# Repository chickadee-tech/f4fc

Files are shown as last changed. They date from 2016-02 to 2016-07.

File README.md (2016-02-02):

# Chickadee Tech F4FC #
This an STM32F4-based flight control Polystack board for multirotors designed by Chickadee Tech. It features an STM32F405VGT6 microcontroller and an MPU-6000 accelerometer/gyroscope. It runs a modified version of [Betaflight](https://github.com/betaflight/betaflight) available [here](github.com/chickadee-tech/betaflight) with the CKD_F4FC target.

## Documentation ##
See the [wiki](https://github.com/chickadee-tech/f4fc/wiki) for documentation.

## Polystack ##
This **control** board is part of the Polystack platform for modular microcontrol systems. More information on the platform can be found at [polystack.org](http://polystack.org).

## Support ##
If you need support with a board you own or have development questions please email support@chickadee.tech or check [chickadee.tech/support](https://chickadee.tech/support) for other ways to get support.

## Contributing ##
Please note that this project is released with a [Contributor Code of Conduct](CODE_OF_CONDUCT.md). By participating in this project you agree to abide by its terms.

### Setup ###
Components and footprints for PCB parts are not included in this repository. Instead, checkout the [chickadee-tech/kicad-libs](https://github.com/chickadee-tech/kicad-libs) repository in the same directory that this repository is checked out in. All part definitions should be relative so that they will load correctly.

### Pull requests ###
For fixes please submit a pull request to the original repository. After the pull request is merged, check the [Chickadee Tech Active Contributor Discount (ACD)](https://chickadee.tech/active-contributor) to see if you are eligible for a discount code to use on your next purchase.

### Derivatives ###
If developing your own version of the F4FC please remove all Chickadee Tech trademarks and follow the [CC-BY license](LICENSE). While not required, please consider open sourcing your modifications so others can learn from your improvements. If you do email support@chickadee.tech and we may choose to add your project to the ACD.

You may also license the Polystack logo for free by emailing support@chickadee.tech. We'll ask for your gerbers to ensure the design complies with specifications laid out [here](https://github.com/chickadee-tech/polystack/wiki) and provide written permission to use the trademark after compliance has been demonstrated.

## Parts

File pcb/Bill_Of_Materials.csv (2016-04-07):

part name | symbol | size (imp) | max current | unit price | units per build | units in stock | On Order | order total | Manufacturer ID | source url | MacroFab HP | datasheet | datasheet2
C 0.1uF | C1, C4, C6, C7, C8, C10, C13 | 603 |  | $0.02 | 7 | 400 | SMD Binder - Capacitors | $0.15 | C0603C104K4RACTU | http://www.digikey.com/product-detail/en/C0603C104K4RACTU/399-1096-1-ND/411371 |  | MF-CAP-0603-0.1uF | http://www.kemet.com/docfinder?Partnumber=C0603C104K4RACTU
C 4.7uF | C2 |  |  | $0.05 | 1 | 8 | SMD Binder - Capacitors | $0.05 | C0603C475K9PACTU | http://www.digikey.com/product-detail/en/C0603C475K9PACTU/399-3482-1-ND/754775 | http://www.mouser.com/ProductDetail/Kemet/C0603C475K9PACTU/ | N
C 2.2nF (2200pF) X7R 50V | C3 | 603 |  | $0.01 | 1 | 94 | SMD Binder - Capacitors | $0.01 | C0603C222K5RACTU | http://www.digikey.com/product-detail/en/C0603C222K5RACTU/399-1085-1-ND/411360 | http://www.mouser.com/ProductDetail/Kemet/C0603C222K5RACTU/?qs=sGAEpiMZZMs0AnBnWHyRQFqPnX0OlvcoEeor2YsHDUE%3d | N
C 2.2uF | C9, C14, C15 | 603 |  | $0.05 | 3 | 92 | SMD Binder - Capacitors | $0.14 | C0603C225K9PACTU | http://www.digikey.com/product-detail/en/C0603C225K9PACTU/399-3362-1-ND/650351 | http://www.mouser.com/ProductDetail/Kemet/C0603C225K9PACTU/?qs=sGAEpiMZZMs0AnBnWHyRQJIiGvDVk92V8FIBbbmgLZk%3d
C 1uF X7R | C5, C12 | 603 |  | $0.03 | 2 | 20 | SMD Binder - Capacitors | $0.06 | TMK107B7105KA-T | http://www.digikey.com/product-detail/en/TMK107B7105KA-T/587-2984-1-ND/2714177 |  | MF-CAP-0603-1uF | http://ds.yuden.co.jp/TYCOMPAS/ut/detail.do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
C 10uF X5R | C11 | 1206 |  | $0.24 | 1 | 80 | SMD Binder - Capacitors | $0.24 | C3216X5R1C106M160AA | http://www.digikey.com/product-detail/en/C3216X5R1C106M160AA/445-1426-1-ND/569092 |  | MF-CAP-1206-10uF | http://product.tdk.com/en/catalog/datasheets/mlcc_commercial_general_en.pdf
red led | D3, D5 |  |  | $0.19 | 2 | 71 | SMD Binder - Diodes | $0.37 | LTST-C190KRKT | http://www.digikey.com/product-detail/en/LTST-C190KRKT/160-1436-1-ND/386816 |  | MF-LED-0603-RED | http://optoelectronics.liteon.com/upload/download/DS-22-99-0151/S_110_LTST-C190KRKT.pdf
yellow led | D2 |  |  | $0.20 | 1 | 87 | SMD Binder - Diodes | $0.20 | LTST-C190KSKT | http://www.digikey.com/product-detail/en/LTST-C190KSKT/160-1437-1-ND/386818 |  | N | http://optoelectronics.liteon.com/upload/download/DS-22-99-0189/S_110_LTST-C190KSKT.pdf
green led | D1 |  |  | $0.19 | 1 | 83 | SMD Binder - Diodes | $0.19 | LTST-C190KGKT | http://www.digikey.com/product-detail/en/LTST-C190KGKT/160-1435-1-ND/386814 |  | Y | http://optoelectronics.liteon.com/upload/download/DS22-2000-074/S_110_LTST-C190KGKT.pdf
Power OR Diode | D4 |  | 500mA | $0.49 | 1 | 6 | SMD Binder - Diodes | $0.49 | PMEG2005CT,215 | http://www.digikey.com/product-detail/en/PMEG2005CT,215/568-6500-1-ND/2531787 | http://www.mouser.com/ProductDetail/NXP/PMEG2005CT215/ | N | http://www.nxp.com/documents/data_sheet/PMEG2005CT.pdf
~3.5mm Spacer | Off Board |  |  | $0.08 | 4 | 81 | SMD Binder - Connectors | $0.33 | 908-140 | http://www.mouser.com/search/ProductDetail.aspx?R=0virtualkey0virtualkey908-140 |  | N
Nylon Hex Nut | Off Board |  |  | $0.10 | 8 | 94 | SMD Binder - Connectors | $0.76 | 4688 | http://www.mouser.com/ProductDetail/Keystone-Electronics/4688/ |  | N
usb otg | P3 |  | 500mA | $0.46 | 1 | 7 | SMD Binder - Connectors | $0.46 | 10118193-0001LF | http://www.digikey.com/product-detail/en/10118193-0001LF/609-4616-1-ND/2785380 | http://www.mouser.com/ProductDetail/FCI/10118193-0001LF/ | MF-CON-MICROUSB-RIGHT
2x4 right angle | P4 |  |  | $0.80 | 1 | 2 | SMD Binder - Connectors | $0.80 | 5-102975-4 |  | http://www.mouser.com/ProductDetail/TE-Connectivity-AMP/5-102975-4/ | N
80 pin receptacle (3.5mm) | CKD_SANDWICH |  | 0.3A a pin | $2.42 | 1 | 1 | SMD Binder - Connectors | $2.42 | DF40HC(3.5)-80DS-0.4V(51) | http://www.digikey.com/product-detail/en/DF40HC(3.5)-80DS-0.4V(51)/H11997CT-ND/2880228 | http://www.mouser.com/ProductDetail/Hirose-Electric/DF40HC35-80DS-04V51/ | N | http://www.hirose.co.jp/cataloge_hp/ed_DF40_20140305.pdf
20pin hirose header | P5 |  | 0.3A a pin | $0.79 | 1 | 7 | SMD Binder - Connectors | $0.79 | DF40C-20DP-0.4V(51) | http://www.digikey.com/product-detail/en/DF40C-20DP-0.4V(51)/H11618CT-ND/1969498 | http://www.mouser.com/ProductDetail/Hirose-Electric/DF40C-20DP-04V51/ | N | http://www.hirose.co.jp/cataloge_hp/ed_DF40_20140305.pdf
Chickadee F4FC v1 | PCB |  |  | $6.73 | 1 | 3 | PCB | $6.73 | CKD-F4FC-V1 |  |  | N
p-channel mosfet | Q1 | TO-236-3, SC-59, SOT-23-4 | 220mA continuous | $0.10 | 1 | 97 | SMD Binder - ICs | $0.10 | BSS84 | http://www.digikey.com/product-detail/en/fairchild-semiconductor/BSS84/BSS84CT-ND/244297 | http://www.mouser.com/search/ProductDetail.aspx?R=0virtualkey0virtualkeyBSS84 | MF-DSC-SOT233-BSS84 | https://www.fairchildsemi.com/datasheets/BS/BSS84.pdf
n-channel mosfet | Q3, Q4 | TO-236-3, SC-59, SOT-23-3 | 220mA continuous | $0.09 | 2 | 59 | SMD Binder - ICs | $0.19 | BSS138 | http://www.digikey.com/product-detail/en/BSS138/BSS138CT-ND/244294 |  | MF-DSC-SOT233-BSS138 | https://www.fairchildsemi.com/datasheets/BS/BSS138.pdf
R 1k | R1, R2, R3, R12 | 603 |  | $0.01 | 4 | 993 | SMD Binder - Resistors | $0.04 | RC0603FR-071KL | http://www.digikey.com/product-detail/en/RC0603FR-071KL/311-1.00KHRCT-ND/729790 |  | MF-RES-0603-1K | http://www.yageo.com/NewPortal/yageodocoutput?fileName=/pdf/R-Chip/PYu-RC_Group_51_RoHS_L_3.pdf
R 10k | R4, R5, R8 | 603 |  | $0.01 | 3 | 979 | SMD Binder - Resistors | $0.03 | RC0603FR-0710KL | http://www.digikey.com/product-detail/en/RC0603FR-0710KL/311-10.0KHRCT-ND/729827 |  | MF-RES-0603-10K | http://www.yageo.com/NewPortal/yageodocoutput?fileName=/pdf/R-Chip/PYu-RC_Group_51_RoHS_L_3.pdf
R 4.7k | R6, R7 | 1206 |  | $0.01 | 2 | 68 | SMD Binder - Resistors | $0.01 | RC0603FR-074K7L | http://www.digikey.com/product-detail/en/RC0603FR-074K7L/311-4.70KHRCT-ND/730159 |  | MF-RES-0603-5.6K | http://www.yageo.com/NewPortal/yageodocoutput?fileName=/pdf/R-Chip/PYu-RC_Group_51_RoHS_L_3.pdf
R 470k | R9 | 603 |  | $0.01 | 1 | 68 | SMD Binder - Resistors | $0.01 | RC0603FR-07470KL | http://www.digikey.com/product-detail/en/RC0603FR-07470KL/311-470KHRCT-ND/730204 |  | MF-RES-0603-470K | http://www.yageo.com/NewPortal/yageodocoutput?fileName=/pdf/R-Chip/PYu-RC_Group_51_RoHS_L_3.pdf
R 100k | R10 | 603 |  | $0.01 | 1 | 55 | SMD Binder - Resistors | $0.01 | RC0603FR-07100KL | http://www.digikey.com/product-detail/en/RC0603FR-07100KL/311-100KHRCT-ND/729836 |  | MF-RES-0603-100K | http://www.yageo.com/NewPortal/yageodocoutput?fileName=/pdf/R-Chip/PYu-RC_Group_51_RoHS_L_3.pdf
reset- side switch | SW1 | EVQ-P7A |  | $0.69 | 1 | 7 | SMD Binder - Misc | $0.69 | EVQ-P7A01P | http://www.digikey.com/product-detail/en/EVQ-P7A01P/P16763CT-ND/4429456 | http://www.mouser.com/ProductDetail/Panasonic/EVQ-P7A01P/ | N | http://media.digikey.com/pdf/Data%20Sheets/Panasonic%20Electronic%20Components/EVQP(7,3,9P7).pdf
acc/gyro | U1 | 24pin QFN 4x4 |  | $10.72 | 1 | 4 | SMD Binder - ICs | $10.72 | MPU-6000 | http://www.digikey.com/product-detail/en/MPU-6000/1428-1005-1-ND/4038006 |  | N | http://store.invensense.com/datasheets/invensense/MPU-6050_DataSheet_V3%204.pdf
STM32F405 | U2 | 100LQFP |  | $10.63 | 1 | 2 | SMD Binder - ICs | $10.63 | STM32F405VGT6 | http://www.digikey.com/product-detail/en/STM32F405VGT6/497-11910-ND/2757670 | http://www.mouser.com/ProductDetail/STMicroelectronics/STM32F405VGT6/ | N | http://www.st.com/web/en/resource/technical/document/datasheet/DM00037051.pdf | Total Price | $37.81
3.3v regulator | U3 | SOT23-5 | 0.3A | $0.49 | 1 | 8 | SMD Binder - ICs | $0.49 | TLV70233DBVR | http://www.digikey.com/product-detail/en/TLV70233DBVR/296-32415-1-ND/3505572 | http://www.mouser.com/ProductDetail/Texas-Instruments/TLV70233DBVR/?qs=sGAEpiMZZMu%2feW%252ba9Wiy7YTpE8hEJFai | MF-REG-SOT235-3.3V-300mA | http://www.ti.com/lit/ds/symlink/tlv702.pdf
8mhz resonator | X1 |  |  | $0.38 | 1 | 8 | SMD Binder - Misc | $0.38 | CSTCE8M00G55-R0 | https://www.digikey.com/product-detail/en/CSTCE8M00G55-R0/490-1195-1-ND/584632 | http://www.mouser.com/ProductDetail/Murata/CSTCE8M00G55-R0/ | N | http://www.murata.com/~/media/webrenewal/support/library/catalog/products/timingdevice/ceralock/p16e.ashx
1x2 housing | Off Board |  |  | $0.08 | 4 | 48 | SMD Binder - Connectors | $0.31 | M20-1060200 | http://www.digikey.com/product-detail/en/M20-1060200/952-2227-ND/3728191 | http://www.mouser.com/ProductDetail/Harwin/M20-1060200/ | N

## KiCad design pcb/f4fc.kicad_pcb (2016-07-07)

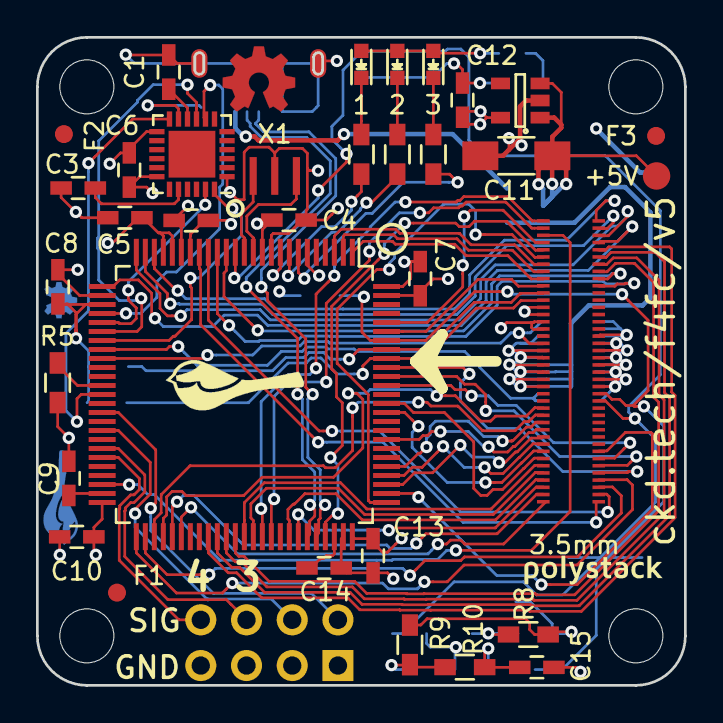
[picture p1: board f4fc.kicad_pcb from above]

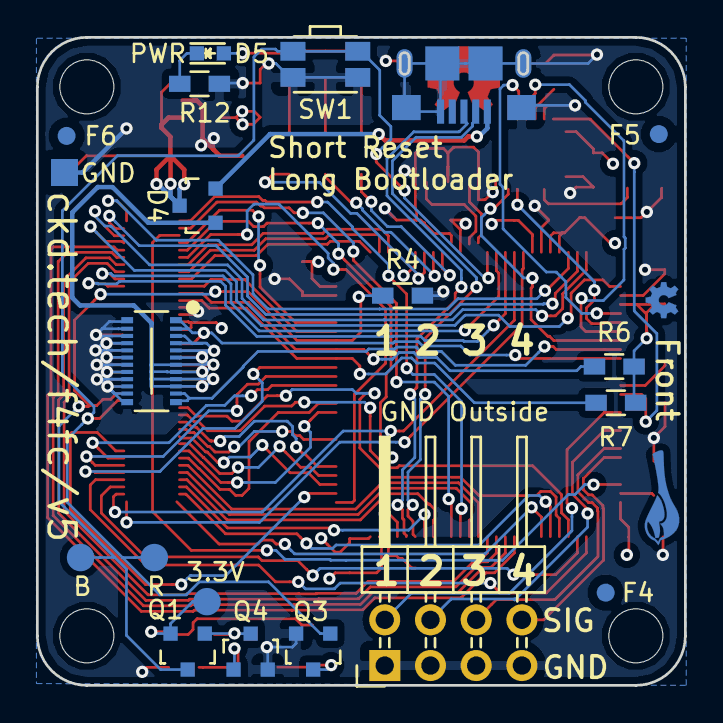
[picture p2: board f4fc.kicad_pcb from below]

Board: 4 copper layers, 36.0 x 36.0 mm, 55 parts (20 on the bottom side), 81 nets.

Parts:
C1, C4, C6, C7, C8, C10, C13: 0.1uF; C_0603_HandSoldering
C2: 4.7uF; C_0603_HandSoldering
C3: 2.2nF; C_0603_HandSoldering
C5: 1uF; C_0603_HandSoldering
C9, C14, C15: 2.2uF; C_0603_HandSoldering
C11: 10uF+; C_1206_HandSoldering
C12: 1uF+; C_0603_HandSoldering
D1: Green; LED_0603
D2: Yellow; LED_0603
D3, D5: Red; LED_0603
D4: D_Schottky_x2_KCom_AAK; SOT-23
F1, F2, F3, F4, F5, F6: 1mm; Fiducial
P1: 3V3; Measurement_Point_Round-SMD-Pad_Small
P2: CONN_01X01; Measurement_Point_Square-SMD-Pad_Small
P3: USB_OTG; Mini-USB-B-EDGE
P4: CONN_02X04; Pin_Header_Angled_2x04
P5: CONN_02X10; DF40-20pin-Header
P6: RESET; Measurement_Point_Round-SMD-Pad_Small
P7: BOOT0; Measurement_Point_Round-SMD-Pad_Small
P9: 5V; Measurement_Point_Round-SMD-Pad_Small
PORT_OUT1: CKD_SANDWICH; DF40-3-4mm-80pin-Receptacle
Q1: Q_PMOS_GSD; SOT-23
Q3, Q4: Q_NMOS_GSD; SOT-23
R1, R2, R3, R12: 1k; R_0603_HandSoldering
R4, R5, R8: 10k; R_0603_HandSoldering
R6, R7: 4.7k; R_0603_HandSoldering
R9: 470k; R_0603_HandSoldering
R10: 100k; R_0603_HandSoldering
SW1: SW_PUSH; SW_SPST_EVQP7A
U1: MPU-6000; QFN-24-1EP_4x4mm_Pitch0.5mm
U2: STM32F40xxx; LQFP-100_14x14mm_Pitch0.5mm
U3: TLV70233DBV; SOT-23-5
X1: 8mhz; CSTCE_G-CSTCE_G_Z
svg2mod: G***; polystack-bold-0.4

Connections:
+5V: D4.1, P5.3, P5.5, P5.7, P5.9, P5.11, P5.13, P5.15, P5.17, PORT_OUT1.19, PORT_OUT1.20, PORT_OUT1.21, PORT_OUT1.22, PORT_OUT1.23, PORT_OUT1.24
+5VA: D4.2, P3.1
+BATT: P5.19, PORT_OUT1.18, U2.34
/ADC1: PORT_OUT1.49, U2.15
/ADC2: PORT_OUT1.50, U2.16
/GPIO1_14_SWCLK: PORT_OUT1.6, U2.76
/GPIO2_13_SWDIO: PORT_OUT1.5, U2.72
/GPIO3: PORT_OUT1.7, U2.3
/GPIO4: PORT_OUT1.8, U2.2
/GPIO5: PORT_OUT1.9, U2.1
/GPIO6: PORT_OUT1.10, U2.95
/LED0: R3.1, U2.7
/LED1: R2.1, U2.8
/LED2: R1.1, U2.9
/MPU_INT: U1.12, U2.38
/MPU_MISO: U1.9, U2.31
/MPU_MOSI: U1.24, U2.32
/MPU_NSS: U1.8, U2.29
/MPU_SCK: U1.23, U2.30
/Power/CURRENT: P5.1, U2.33
/Reset/BOOT0: P7.1, PORT_OUT1.65, Q1.3, R4.2, U2.94
/Reset/RESET: P6.1, PORT_OUT1.66, Q3.1, SW1.2, U2.14
/SPI1_MISO: PORT_OUT1.79, U2.17
/SPI1_MOSI: PORT_OUT1.80, U2.18
/SPI1_NSS: PORT_OUT1.77, U2.51
/SPI1_SCK: PORT_OUT1.78, U2.52
/SPI2_MISO: PORT_OUT1.75, U2.90
/SPI2_MOSI: PORT_OUT1.76, U2.91
/SPI2_NSS: PORT_OUT1.73, U2.77
/SPI2_SCK: PORT_OUT1.74, U2.89
/TIM1_CH1: P4.2, U2.40
/TIM1_CH2: P4.4, U2.42
/TIM1_CH3: P4.6, U2.44
/TIM1_CH4: P4.8, U2.45
/TIM2_CH4: PORT_OUT1.3, U2.48
/TIM3_CH4: PORT_OUT1.2, U2.66
/TIM8_CH3: PORT_OUT1.1, U2.65
/TIM11_CH1: PORT_OUT1.4, U2.96
/TIM12_CH1_UART8_RX: PORT_OUT1.28, U2.53
/TIM12_CH2_UART8_TX: PORT_OUT1.27, U2.54
/TIMG1_CH1: PORT_OUT1.41, U2.23
/TIMG1_CH2: PORT_OUT1.42, U2.24
/TIMG1_CH3: PORT_OUT1.43, U2.25
/TIMG1_CH4: PORT_OUT1.44, U2.26
/TIMG2_CH1: PORT_OUT1.45, U2.59
/TIMG2_CH2: PORT_OUT1.46, U2.60
/TIMG2_CH3: PORT_OUT1.47, U2.61
/TIMG2_CH4: PORT_OUT1.48, U2.62
/UART1_RX: PORT_OUT1.38, U2.69
/UART1_TX: PORT_OUT1.37, U2.68
/UART2_RX: PORT_OUT1.34, U2.87
/UART2_TX: PORT_OUT1.33, U2.86
/UART3_RX: PORT_OUT1.40, U2.56
/UART3_TX: PORT_OUT1.39, U2.55
/UART4_RX: PORT_OUT1.32, U2.79
/UART4_TX: PORT_OUT1.31, U2.78
/UART5_RX: PORT_OUT1.30, U2.83
/UART5_TX: PORT_OUT1.29, U2.80
/UART6_RX: PORT_OUT1.36, U2.64
/UART6_TX: PORT_OUT1.35, U2.63
/USB_D+: P3.3, U2.71
/USB_D-: P3.2, U2.70
/i2c_SCL: PORT_OUT1.12, R7.2, U2.92
/i2c_SDA: PORT_OUT1.11, R6.1, U2.93
GNDPWR: C1.2, C2.1, C3.1, C4.1, C5.1, C6.2, C7.1, C8.1, C9.2, C10.2, C11.2, C12.2, C13.1, C14.1, C15.2, P2.1, P3.5, P3.6, P4.1, P4.3, P4.5, P4.7, P5.2, P5.4, P5.6, P5.8, P5.10, P5.12, P5.14, P5.16, P5.18, P5.20, PORT_OUT1.13, PORT_OUT1.14, PORT_OUT1.57, PORT_OUT1.58, PORT_OUT1.59, PORT_OUT1.60, PORT_OUT1.61, PORT_OUT1.62, PORT_OUT1.63, PORT_OUT1.64, Q3.2, Q4.2, R4.1, R5.2, R12.2, SW1.1, U1.1, U1.11, U1.18, U2.10, U2.20, U2.27, U2.74, U2.99, U3.2, X1.3
unnamed: C1.1, U1.10
unnamed: C3.2, U1.20
unnamed: C9.1, U2.49
unnamed: C11.1, D4.3, P9.1, U3.1, U3.3
unnamed: C14.2, U2.73
unnamed: C15.1, Q4.1, R10.1
unnamed: D1.1, R1.2
unnamed: D2.1, R2.2
unnamed: D3.1, R3.2
unnamed: D5.1, R12.1
unnamed: Q1.1, Q4.3, R8.2
unnamed: Q3.3, R9.2, R10.2
unnamed: R5.1, U2.37
unnamed: U2.12, X1.1
unnamed: U2.13, X1.2
VDD: C2.2, C4.2, C5.2, C6.1, C7.2, C8.2, C10.1, C12.1, C13.2, D1.2, D2.2, D3.2, D5.2, P1.1, PORT_OUT1.15, PORT_OUT1.16, Q1.2, R6.2, R7.1, R8.1, R9.1, U1.13, U2.6, U2.11, U2.19, U2.21, U2.22, U2.28, U2.50, U2.75, U2.100, U3.5

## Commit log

2016-02-02 v1 of F4FC. Similar layout to F3FC but with an F4 chip. It has a higher clock speed and one more UART.
    [Bill_Of_Materials.csv, ExpansionPort.sch, Power.sch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]
2016-03-05 F4FC v2 featuring corrected reset circuit.
    Other changes:
    * Route USB as differential pair.
    * Add fiducials
    * Remove copper pour from power connector
    * New reset circuit
    * Match up led nubmering to references
    * Support current sensor through power connector
    * remove 1.5k pull up from USB
    * Pull down Boot1
    * Add OSHW logo
    * Move 3.5mm label out form under the FlightStack connector.
    [Bill_Of_Materials.csv, Power.sch, Reset.sch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]
2016-04-07 More changes to F4. Can't remember what.
    [Bill_Of_Materials.csv, Power.sch, Reset.sch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]
2016-04-13 Rebrand everything to Polystack and increment versions.
    [f4fc.kicad_pcb]
2016-04-16 Final gerbers for test manufacturing run.
    [f4fc-B.Cu.gbl, f4fc-B.Mask.gbs, f4fc-B.Paste.gbp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]
2016-06-07 Update polystack logo to bold variant and bump version number.
    [f4fc.kicad_pcb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]
2016-07-07 Add license information to many files. PCB design files are CC-BY and code is MIT license.
    [Power.sch, Reset.sch, f4fc.kicad_pcb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]
2016-07-07 Convert to relative component and footprint paths.
    [ExpansionPort.sch, Power.sch, Reset.sch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]

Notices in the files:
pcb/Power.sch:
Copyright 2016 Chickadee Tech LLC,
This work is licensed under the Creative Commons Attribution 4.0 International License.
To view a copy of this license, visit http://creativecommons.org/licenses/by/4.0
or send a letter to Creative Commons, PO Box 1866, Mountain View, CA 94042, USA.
